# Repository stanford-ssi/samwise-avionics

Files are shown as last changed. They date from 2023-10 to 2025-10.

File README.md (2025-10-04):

# SAMWISE Avionics Repository
Welcome to the SAMWISE GitHub Avionics repository! Here, we (try to) keep the most updated versions of all of our circuit boards accessible to the public.
[Link to the Wiki for onboarding info and general resources](https://github.com/stanford-ssi/samwise-wiki/wiki/Avionics)

## General Layout
Individual boards have their own folders to ease merging of branches. Symbol libraries, footprint libraries, and 3D models are in separate top-level folders. Project templates (for starting out) and jobsets (for project export) are in other top-level folders. Unused, old boards are in the unused_boards folder.

## KiCad Version: 9.0.1 ≤ V < 10.0
Exception: unused boards are version 8.X.X

## List of Relevant Boards (in alphabetical order of folder name)
Note that each major revision generally indicates a new satellite or a significant overhaul of the board and each minor revision generally indicates a board order.
| Board Name | Folder Name |  Current Rev  |  Current Rev Gerber Date  |  Brief Description
| --- | --- | --- | ---  | ---
| ADCS | ADCS/ADCS-v1-samwise  | 01.8 | 09/21/25 | Attitude Control Determination System (ADCS) controller board
| Reaction Wheel Motor Board | ADCS/ADCS-motors-v1-samwise  | 01.1 | 05/28/25 | ADCS reaction wheel controller board
| Battery Board | BatteryBoard | 02.3 | 04/05/25 | Contains battery, charging IC. 2x per satellite
| Flex Deploy Side Panels | FlexDeploySidePanels | 03.3 | 04/22/25 | Deployable side panels, on SAMWISE Y sides (2 sides)
| Groundstation 433 MHz HAT  | Groundstation_433_Hat | 01.3 | 04/07/25 | Raspberry Pi HAT control board for 433 MHz groundstation
| Groundstation 2400 MHz HAT | Groundstation_2400_Hat | 01.6 | 04/06/25 | Raspberry Pi HAT control board for 2400 MHz groundstation
| LT8491 MPPT Module | LT8491_mezzanine | 01.1 | 04/05/25 | Maximum power point tracking (MPPT) module, adapted from Max Holliday's design
| PiCubed | PiCubed/mainboard-v06.4_samwise | 06.4 | 09/21/25 | SAMWISE's master controller board
| MPPT Add-on Board | PiCubed/MPPT_addon_board | 01.4 | 04/06/25 | Holds MPPT modules, attaches to PiCubed
| RPi Interface Board | RPi_Interface | 01.3 | 04/07/25 | HAT board for Raspberry Pi+camera system and 2400 MHz radio
| Stationary X Side Panels | Stationary_X_Panel | 01.6 | 04/26/25 | Stationary (fixed) side panels, on SAMWISE X sides (2 sides)
| Sun Pyramid | sun_sensor_pyramid | 03.2 | 04/07/25 | Holds sun sensors that help determine sun vector for ADCS system
| XY Magnetorquer Coils | Universal_XY_MagTorq | 02.2 | 04/26/25 | XY magnetorquer coil boards, 2 per XY side (4 sides total) in parallel and 5 coils/board in series
| Z Magnetorquer Coils | Universal_Z_MagTorq | 01.1 | 04/07/25 | Z magnetorquer coil boards, 2 per Z side (2 sides total) in parallel and 5 coils/board in series
| Z Side Panel | ZPlus_Panel | 02.4 | 04/22/25 | Z side panels, with antenna + camera on Z+ side. For both Z+ and Z- after thruster removed from Z-

## Guidelines
1. Set up KiCad and GitHub according to the guides in the Wiki.
2. ALWAYS check via `git status` and pull via `git pull` BEFORE making edits. If going into someone else's branch or main, use `git restore <file>` to restore changes before returning to your branch and do NOT commit/push changes without the branch owner's explicit permission. 
3. Create your own branch when making edits. Make pull requests when you have finalized your changes. Do NOT push to main unless you are an AV or team co-lead.
4. To prepare your board for ordering, follow the Board Review and Ordering Procedures linked on the [Notion page](https://ssisatellites.notion.site/Avionics-4ecec69fa093445191cafdee6dff3940). This saves AV/team leads a substantial amount of time, and keeps things consistent/easy to review.
5. Do not edit this README unless you are an AV or team co-lead.

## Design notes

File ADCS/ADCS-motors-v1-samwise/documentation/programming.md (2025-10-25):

Created a repo by forking adcs-flight software
https://github.com/nablaxcroissant/samwise-adcs-motor-flight/tree/main

## I2C Battery Readout
PWR SDA is on pin 45, GPIO 36
PWR SCL is on pin 46, GPIO 37

This means that it lies on I2C bus 0

The IO UART is on GPIO40 for TX and GPIO41 for RX.
This corresponds to UART1 bus.

## may 15 First time testing motor driver code!
The chip enables! Just a SIO gpio pull up and it works as expected.
It draws 21mA at 7V. I'm pretty sure that between 90% and 95% of that is just the driver alone. Could mean that the chip is pulling a lot of power...

I expect it to draw under 10mA at 24V... This means we are good!!!
It is important to note though that this does end up meaning about 80mA power between all 4 motors, even when they are off. When the motors are off its easily fixed - just put them into sleep mode! Will require some extra code probably.

Fault is pulled low...
I figured it out! Its the MOTOR LOCK fault! I just needed to write the spi driver, and it showed me that the 7th bit on register 00 is a motor lock fault. This is probably because the motor is not plugged in.

# Ok that shit is fixed! Was all due to solder issues.

May 30, got SPI communicating!

Now I need to set the correct hall effect configuration
https://shop.faulhaber.com/2610t006b.html
I almost fucked up bad but got really lucky! https://faulhaber.com.cn/fileadmin/Import/Media/AN163_EN.pdf
I was planning to give the hall effects 5V but that could damage the chip. But it looks like 3.3V is actually within the operating range of the hall effects! Yippee!

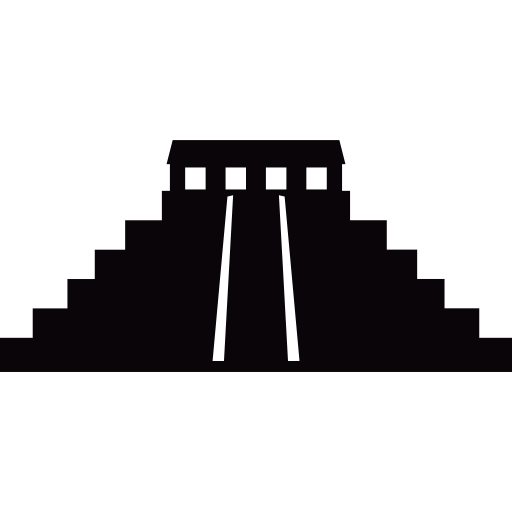
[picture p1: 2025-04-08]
sun_sensor_pyramid/piramide_del_sol.png

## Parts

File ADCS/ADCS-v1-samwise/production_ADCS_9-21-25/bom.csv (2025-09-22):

Designator | Footprint | Quantity | Value | LCSC Part #
C1, C2 | 0603 | 2 | 15pF
C10, C11, C12, C15, C29 | 0603 | 5 | 4.7uF
C13, C14, C16, C21, C23, C28, C31, C35, C37, C42, C43, C44, C45, C46, C47, C5, C59, C60, C63, C7 | 0603 | 20 | 100nF
C17, C18, C24, C33, C9 | 0603 | 5 | 22uF
C19, C20, C22, C25, C30, C34, C38, C39, C48, C51, C66, C8 | 0603 | 12 | 10uF
C26, C32 | 0603 | 2 | 3.3nF
C27, C6, C67 | 0603 | 3 | 1uF
C3, C55, C57, C61, C64 | 0603 | 5 | 10nF
C36, C40, C41, C52, C53, C54 | 0603 | 6 | 3.3uF
C4, C56, C58, C62, C65 | 0603 | 5 | 4.7uF
C49 | 0603 | 1 | 2.2uF
D1 | LED_WS2812B_PLCC4_5.0x5.0mm_P3.2mm | 1 | 1655
D2 | D_SOD-123 | 1 | 1N4151W-E3-08
D3, D4, D6 | DIOM5226X262N | 3 | CMSH1-40M
D5 | 0603 | 1 | GREEN LED
J1, J16, J17, J2 | Molex_505567-0431 | 4 | 505567-0431
J10, J11, J12, J13, J14, J15 | Molex_205338-0002 | 6 | 2053380002
J18, J3 | Molex_505567-0631 | 2 | 505567-0631
J19 | JST_SH_BM04B-SRSS-TB_1x04-1MP_P1.00mm_Vertical | 1 | QWIIC
J20 | SAMTEC_FTSH-105-01-L-DV-007 | 1 | Conn_ARM_JTAG_SWD_10
J4 | Molex_35362-1250 | 1 | 35362-1250
J5 | PinHeader_1x04_P2.54mm_Vertical | 1 | Conn_01x04
J6, J7 | SMA_Amphenol_901-144_horizontal | 2 | Amphenol_901-144
J8 | PinHeader_1x10_P2.54mm_Vertical | 1 | Conn_01x10
J9 | USB_C_Receptacle_XKB_U262-161N-4BVC11 | 1 | USB_C_pycubed
L1 | 0805 | 1 | 3.3uH
L2 | L_2141 | 1 | 3.3uH
Q1, Q2, Q4, Q5, Q6 | DMP2040USS-13 | 5 | DMP2040USS-13
Q3 | SOT-23 | 1 | MMBT2222A
Q7 | SOT-23 | 1 | IRLML2803
R1, R25, R35, R48, R9 | 0603 | 5 | 10k
R10, R11, R12, R15, R53, R56, R64, R65, R66 | 0603 | 9 | 100k
R13 | 0603 | 1 | 73.2k
R14 | 0603 | 1 | 22.1k
R16, R20, R23, R3, R30, R33, R36, R38, R4, R42, R44, R52, R54 | 0603 | 13 | 1k
R17, R21, R22, R29, R31, R32, R34, R37, R41, R43, R45, R46, R5, R50, R51, R59, R6, R60, R61, R68, R70 | 0603 | 21 | 10k
R18 | 0603 | 1 | 5
R2, R24, R47, R8 | 0603 | 4 | 4.7k
R26 | 0603 | 1 | 33
R27, R28 | 0603 | 2 | 27
R39, R40 | 0603 | 2 | 5.1k
R49, R57 | 0603 | 2 | 0
R55 | 0603 | 1 | 4.7M
R62, R63 | 0603 | 2 | 3k
R67 | 0603 | 1 | 4.7k
R69 | 0603 | 1 | 3.3k
R7 | 2512 | 1 | 0.02
SW1, SW2 | BTN_KMR2_4.6X2.8 | 2 | KMR231NG LFS
U1, U6, U8 | QFN-14_MP6551_MNP | 3 | MP6551GQB-Z
U10 | RM3100CB | 1 | RM3100CB
U11 | BMI270 | 1 | BMI270
U12 | Orion_B16 | 1 | Orion B16
U13 | QFN32-5X5MM | 1 | EP2W+
U14, U9 | TSSOP-16_4.4x5mm_P0.65mm | 2 | ADS7830
U15 | SOT-23-5 | 1 | TPS70960DBVR
U2 | RP2350-QFN-80-1EP_10x10_P0.4mm_EP3.4x3.4mm_ThermalVias | 1 | RP2350_80QFN
U3 | SON127P600X500X90-9N | 1 | MR25H40MDF
U4 | ADM1176-1ARMZ-R7 | 1 | RM_10
U5 | PWP14_2P31X2P46-L | 1 | TPS54226PWPR
U7 | TSSOP-14_4.4x5mm_P0.65mm | 1 | TLV1704
Y1 | Crystal_SMD_3225-4Pin_3.2x2.5mm | 1 | ABM8-272-T3

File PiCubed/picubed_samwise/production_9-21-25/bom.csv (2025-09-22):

Designator | Footprint | Quantity | Value | LCSC Part #
C1, C2 | 0603 | 2 | 15pF
C10, C11, C12, C15, C29, C34 | 0603 | 6 | 4.7uF
C13, C14, C16, C21, C24, C28, C3, C40, C45, C46, C47, C48, C49, C5, C50, C7 | 0603 | 16 | 0.1uF
C17, C18, C31, C37, C38 | 0603 | 5 | 22uF
C19, C20, C22 | 1210 | 3 | 10uF
C23, C27, C33, C4 | 0603 | 4 | 1uF
C25, C30, C35, C39, C41, C42, C43, C44, C51, C54, C9 | 0603 | 11 | 10uF
C26, C32 | 0603 | 2 | 3.3nF
C36 | 0603 | 1 | 47nF
C53 | 0603 | 1 | 2.2uF
D1 | LED_WS2812B_PLCC4_5.0x5.0mm_P3.2mm | 1 | 1655
D2 | DO-214AC | 1 | CDBA240LL
D3, D7, D8 | DIOM5226X262N | 3 | CMSH1-40M
D4 | PWRDI-123 | 1 | DFLS130L
D5 | 0603 | 1 | GREEN LED
D6 | D_SOD-123 | 1 | 1N4151W-E3-08
J1 | Molex_503182-1852 | 1 | 503182-1852
J10, J17 | Molex_35362-0450 | 2 | 35362-0450
J11 | PinSocket_2x09_P2.54mm_Vertical | 1 | MPPT board
J12, J15 | Molex_35362-0550 | 2 | 35362-0550
J13 | USB_C_Receptacle_XKB_U262-161N-4BVC11 | 1 | USB_C_pycubed
J14 | PinHeader_1x08_P2.54mm_Horizontal | 1 | Conn_01x08_Horizontal
J16, J18, J8, J9 | 1985807 | 4 | 1985807
J19 | Molex_35362-0650 | 1 | 35362-0650
J2 | SAMTEC_FTSH-105-01-L-DV-007 | 1 | Conn_ARM_JTAG_SWD_10
J20, J21 | Molex_35362-0750 | 2 | 35362-0750
J22 | JST_SH_BM04B-SRSS-TB_1x04-1MP_P1.00mm_Vertical | 1 | QWIIC
J3, J4 | Molex_35362-0850 | 2 | 35362-0850
J5 | Molex_35362-1250 | 1 | 35362-1250
J6 | Molex_35362-0950 | 1 | 35362-0950
J7 | SMA_Amphenol_901-144_horizontal | 1 | Amphenol_901-144
JP1 | SolderJumper-2_P1.3mm_Open_Pad1.0x1.5mm | 1 | Jumper_2_Open
JP2, JP3 | SolderJumper-2_P1.3mm_Bridged_Pad1.0x1.5mm | 2 | Jumper_2_Bridged
L1 | polarized | 1 | 3.3uH
L2 | L_2141 | 1 | 3.3uH
L3 | SDE06004A-680K | 1 | 68uH
L4 | L_2510 | 1 | 1uH
Q10, Q21 | DMP2040USS-13 | 2 | DMP2040USS-13
Q5, Q9 | SOT-23 | 2 | IRLML2803
Q6 | SOT-23 | 1 | MMBT2222A-TP
R1, R18 | 0603 | 2 | 330k
R10 | 0603 | 1 | 20k
R11, R12, R15, R27, R38, R46, R60, R61, R62, R68, R69, R70, R75 | 0603 | 13 | 100k
R13 | 0603 | 1 | 73.2k
R14 | 0603 | 1 | 22.1k
R16 | 0603 | 1 | 49.9k
R17 | 0603 | 1 | 510k
R19 | 2512 | 1 | 0.27
R2 | 0603 | 1 | 110k
R20, R23, R26, R3, R4, R56, R6, R63 | 0603 | 8 | 1k
R21, R22, R25, R28, R29, R31, R34, R35, R44, R45, R5, R51, R53, R54, R55, R57, R71, R72, R73, R74, R76, R77, R78 | 0603 | 23 | 10k
R33, R58, R59 | 0603 | 3 | 3.3k
R36 | 0603 | 1 | 560
R39, R40 | 0603 | 2 | 5.1k
R50, R82 | 0603 | 2 | 0
R64 | 0603 | 1 | 4.7M
R65 | 0603 | 1 | 33
R66, R67 | 0603 | 2 | 27
R79, R80 | 0603 | 2 | 3k
R8 | 2512 | 1 | 0.02
R9 | 0603 | 1 | 121k
SW1, SW2 | BTN_KMR2_4.6X2.8 | 2 | KMR231NG LFS
U1 | SOT-23-5 | 1 | TPS70960DBVR
U16 | Relay_PE014006 | 1 | PE014006
U17 | QFN50P400X400X100-25N-D | 1 | BQ25883RGER
U2 | RP2350-QFN-80-1EP_10x10_P0.4mm_EP3.4x3.4mm_ThermalVias | 1 | RP2350_80QFN
U21 | TPS7A4501DCQT | 1 | TPS7A4501DCQT
U23 | RFM98PW | 1 | RFM98PW
U3 | SON127P600X500X90-9N | 1 | MR25H40MDF
U4 | ADM1176-1ARMZ-R7 | 1 | RM_10
U5 | PWP14_2P31X2P46-L | 1 | TPS54226PWPR
U6 | MSOP-12_MSE | 1 | LT3652HVIMSE#PBF
U7 | TSSOP-14_4.4x5mm_P0.65mm | 1 | TLV1704
Y1 | Crystal_SMD_3225-4Pin_3.2x2.5mm | 1 | ABM8-272-T3

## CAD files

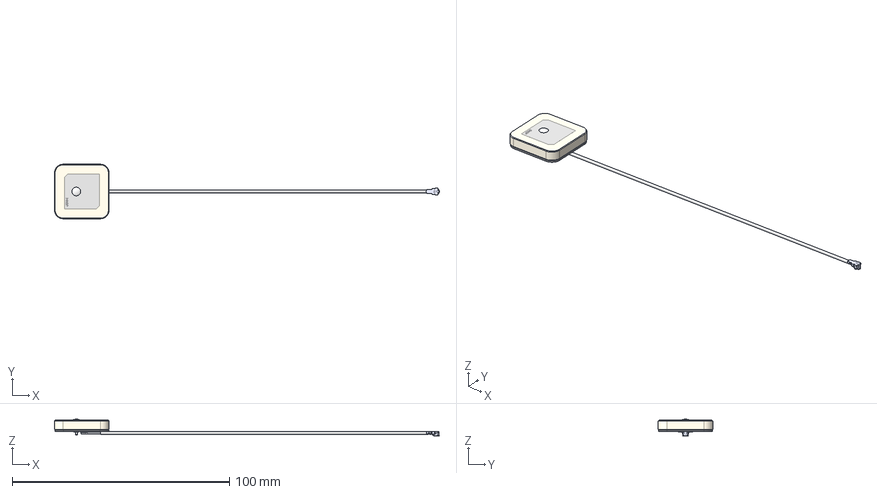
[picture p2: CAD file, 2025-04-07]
3D_models/ssi_antenna/WPC_25A.step
177.0 x 25.1 x 7.67 mm
001517C100000A WLP.2450.25.4 Patch
100211I010011A_WPC.25A PCB
300115C010000A_1.37 Gray Cable
204511G000000A_IPEX MHFHT. 1.37

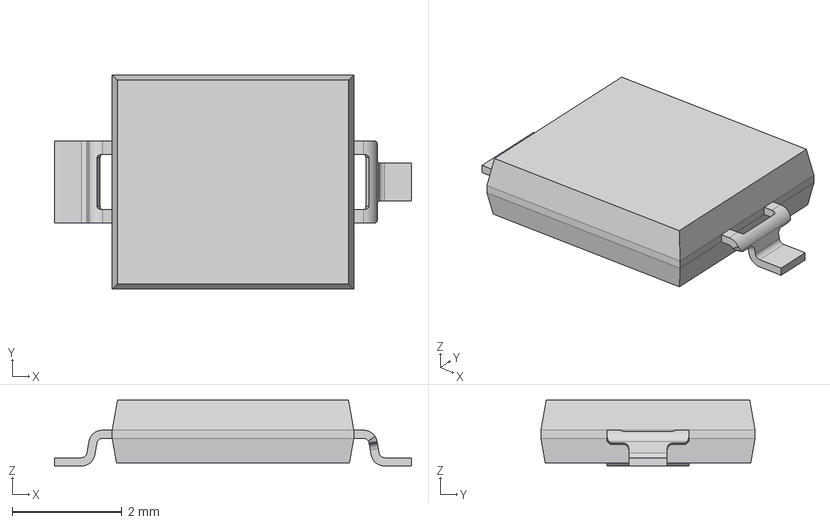
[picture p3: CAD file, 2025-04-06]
3D_models/ssi_diode/SFH_2430.step
6.50 x 3.90 x 1.20 mm

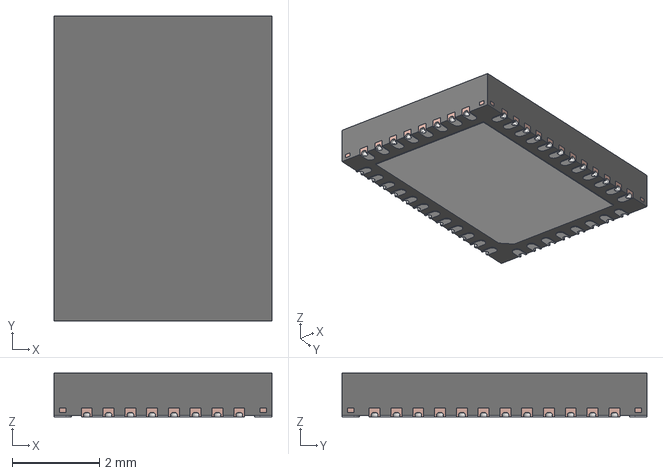
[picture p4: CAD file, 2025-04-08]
3D_models/ssi_IC/MCT8316Z-Q1.step
5.00 x 7.00 x 1.00 mm
FRAME

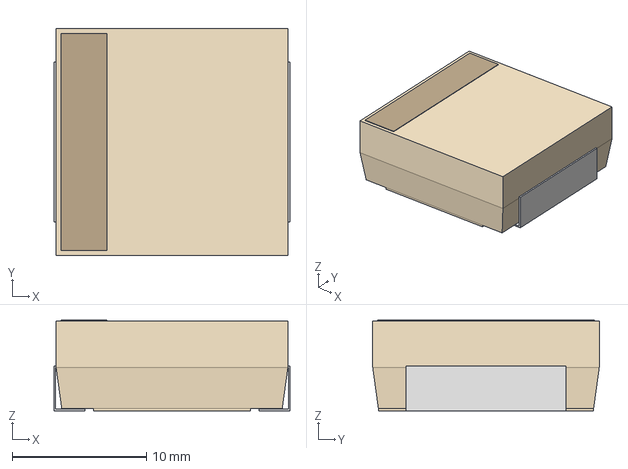
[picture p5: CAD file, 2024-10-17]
3D_models/ssi_inductor/SRP1770CC.step
17.6 x 16.9 x 6.76 mm

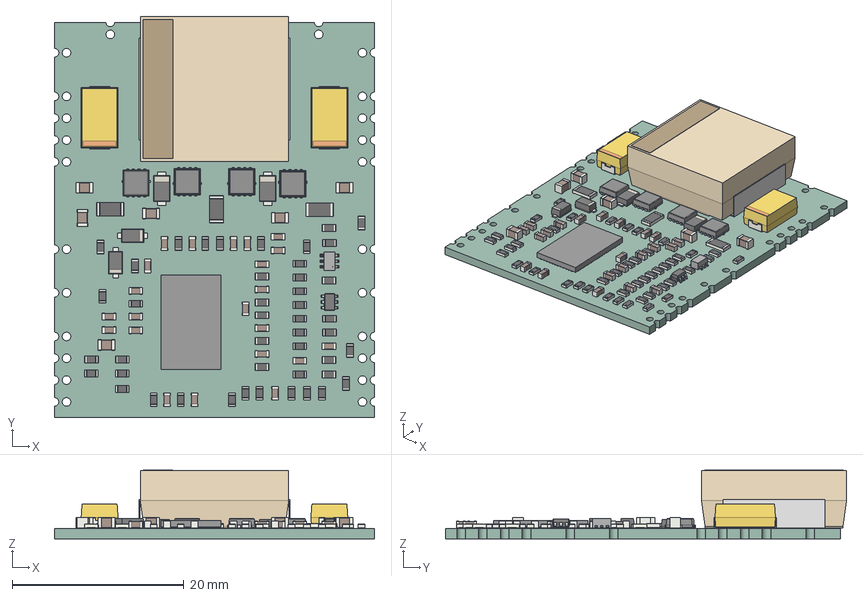
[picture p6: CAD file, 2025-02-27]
3D_models/ssi_misc/LT8491.step
37.2 x 46.7 x 8.02 mm
R_0603_1608Metric x 45
C_0805_2012Metric x 6
C_0603_1608Metric x 22
D_PowerDI_123 x 2
SOT_363_SC_70_6
(Unsaved) x 5
R_1206_3216Metric x 3
D_SOD_123F x 2
CP_EIA_7343_30_AVX_N x 2
LT8491-mezzanine_PCB

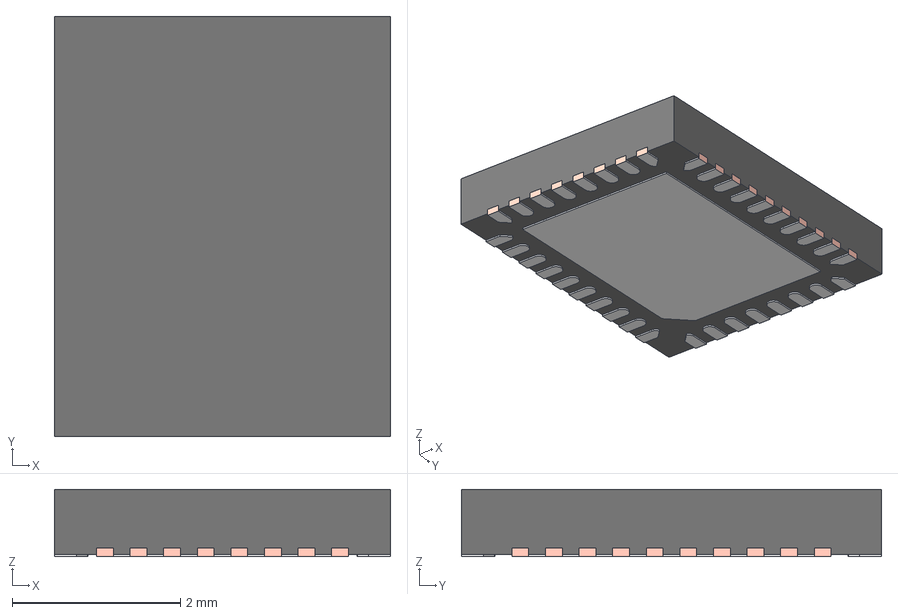
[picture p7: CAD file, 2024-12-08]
3D_models/ssi_reaction_wheel/REE0036A.stp
4.00 x 5.00 x 0.8 mm
BODY-QFN
FRAME-REE0036A

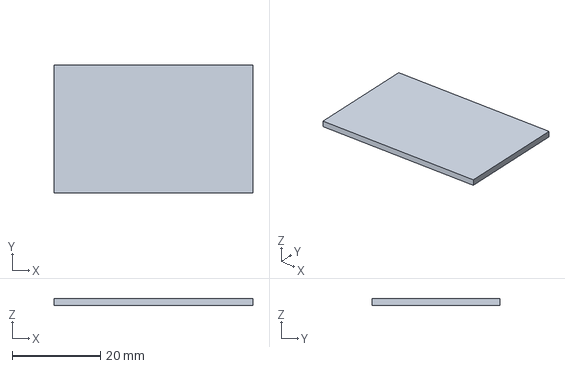
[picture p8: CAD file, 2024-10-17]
3D_models/ssi_solar/SM141K08TFV.step
45.0 x 29.0 x 1.50 mm

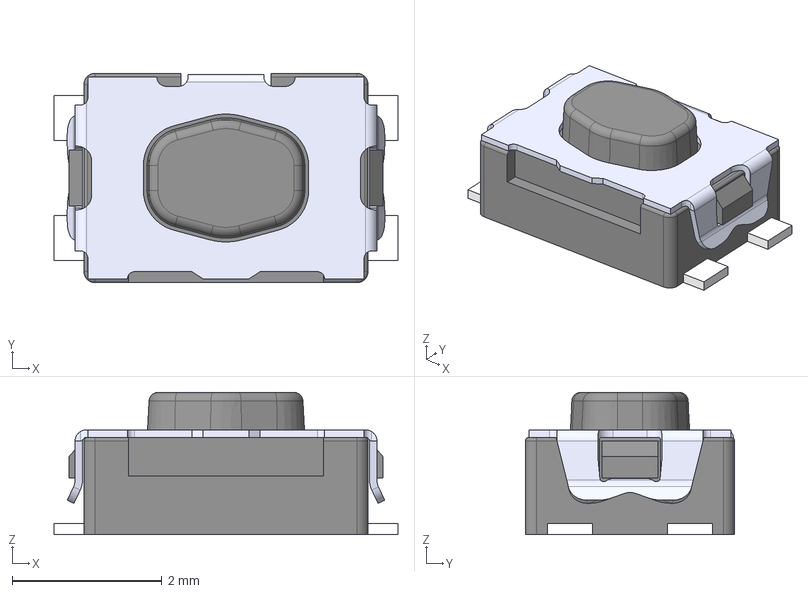
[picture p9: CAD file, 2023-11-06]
3D_models/ssi_switch/KMR221GLFS.step
4.60 x 2.80 x 1.90 mm

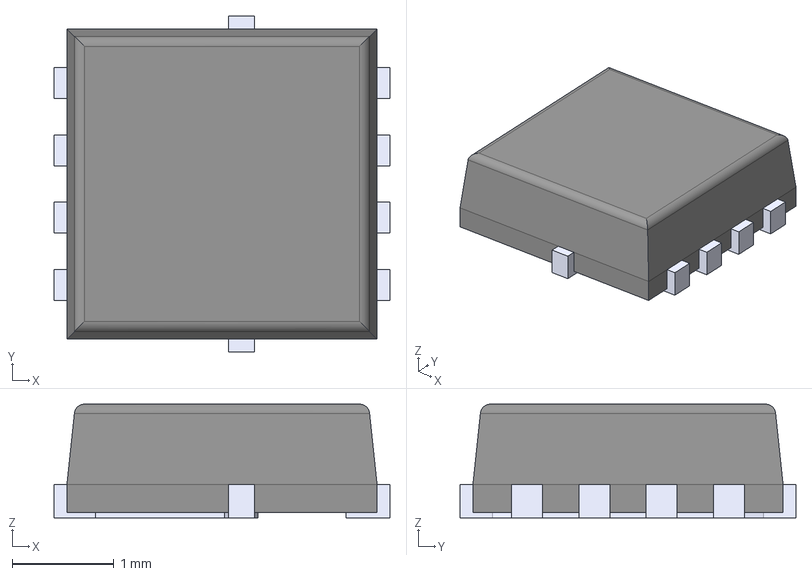
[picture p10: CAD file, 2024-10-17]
3D_models/ssi_transistor/SIS128LDN-T1-GE3.step
3.30 x 3.30 x 1.12 mm

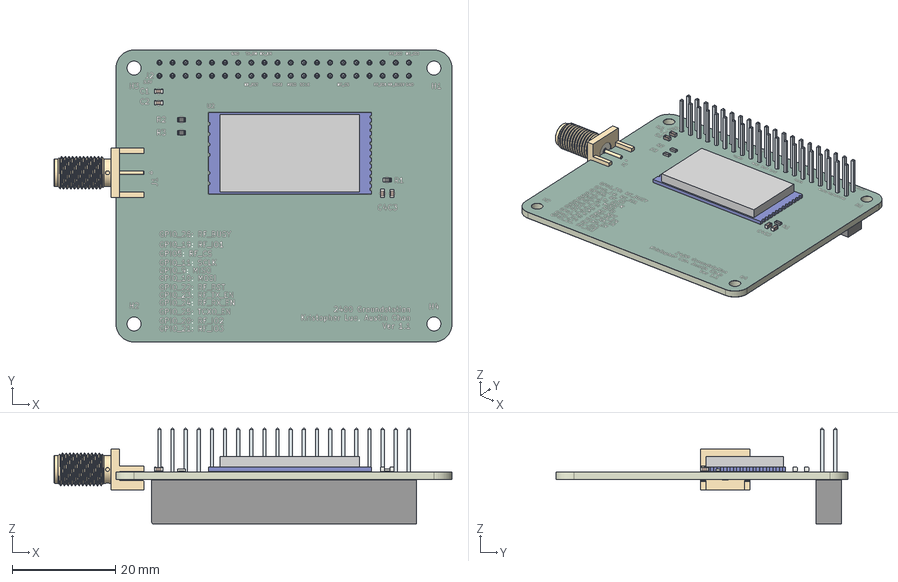
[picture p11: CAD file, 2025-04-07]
Groundstation_2400_Hat/Groundstation_2400_Hat_v1.1_2025-04-06.step
77.0 x 56.5 x 18.5 mm
C_0603_1608Metric x 4
R_0603_1608Metric x 3
LORA1280F27-TCXO
SMA_Amphenol_132289_EdgeMount
LeadsArray
Groundstation_2400_Hat_silkscreen
Groundstation_2400_Hat_soldermask
Groundstation_2400_Hat_PCB

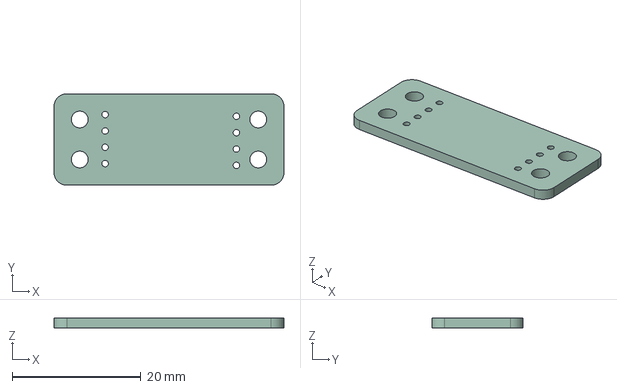
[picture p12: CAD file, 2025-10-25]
magnetometer_extern/magnetometer_extern/magnetometer_extern.step
35.8 x 14.2 x 1.51 mm

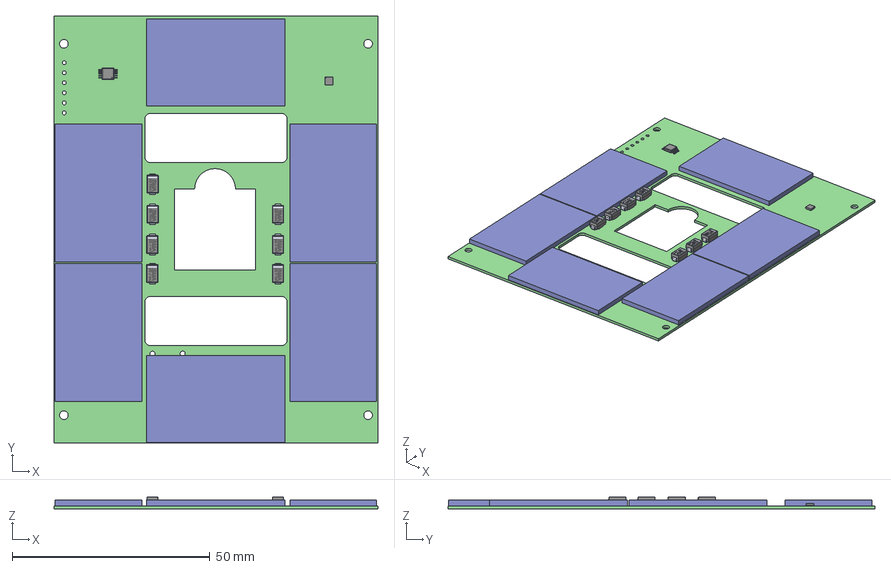
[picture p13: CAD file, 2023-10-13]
MagnetorquerSidePanels/X_Y_Panels.step
82.0 x 108.0 x 3.15 mm
X_Y_Panels PCB

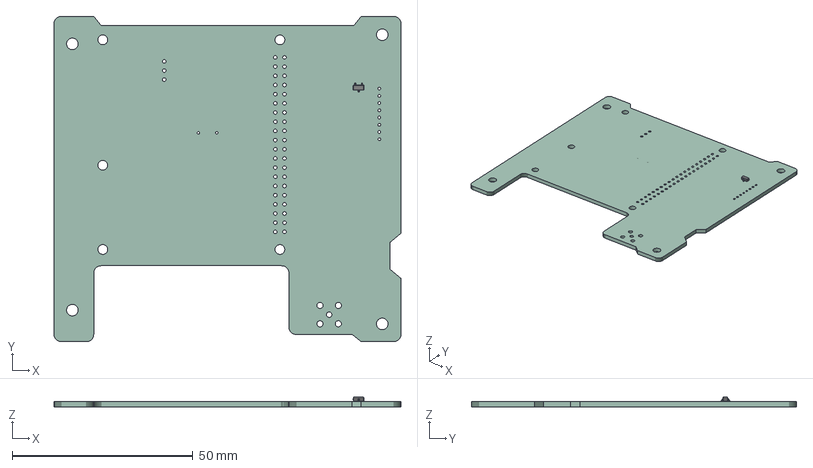
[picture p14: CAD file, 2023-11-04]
RPi_Interface/RPi_interface.step
96.0 x 90.0 x 2.84 mm
RPi_interface PCB

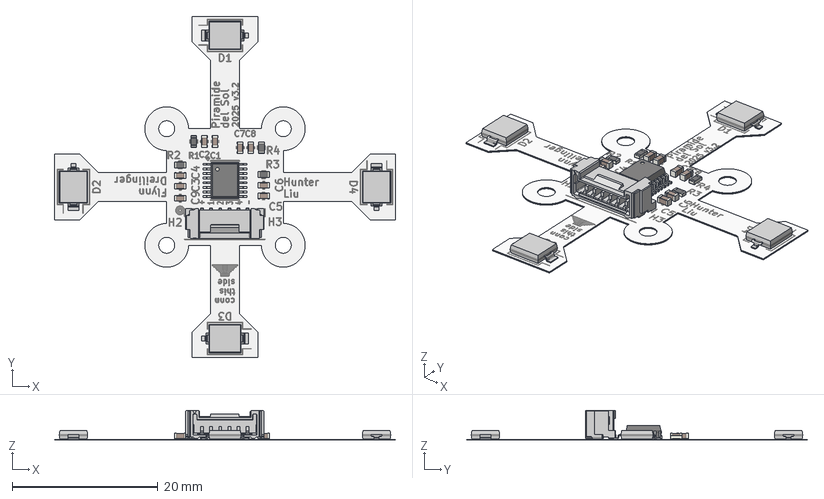
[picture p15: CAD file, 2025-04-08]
sun_sensor_pyramid/Piramide_Del_Sol_v3.2_2025-04-07.step
46.8 x 46.8 x 4.13 mm
SFH_2430 x 4
C_0603_1608Metric x 9
R_0603_1608Metric x 4
SSOP-16_3.9x4.9mm_P0.635mm
Piramide_Del_Sol_silkscreen
Piramide_Del_Sol_soldermask
Piramide_Del_Sol_PCB

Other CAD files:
Universal_XY_MagTorq/Coil_Panel_XY_v2.2_2025-04-26.step
Universal_Z_MagTorq/Coil_Panel_Z_v1/Coil_Panel_Z_v1.1_2025-04-07.step
3D_models/ssi_antenna/AP_25M.step
3D_models/ssi_diode/M7.step
3D_models/ssi_IC/ADM1176-1ARMZ-R7.step
3D_models/ssi_IC/ATSAMD51J20A-AU.step
3D_models/ssi_IC/BMI270.step
3D_models/ssi_IC/DRV8830DGQ.STEP
3D_models/ssi_IC/EP2W.step
3D_models/ssi_IC/HHM1589D1.step
3D_models/ssi_IC/LORA1280F27-TCXO.step
3D_models/ssi_IC/LT8491IUKJ#PBF.step
3D_models/ssi_IC/MP6551GQB-Z.step
3D_models/ssi_IC/MR25H40MDF.step
3D_models/ssi_IC/MSOP-12_MSE_LIT.step
3D_models/ssi_IC/OPT3001DNPT.step
3D_models/ssi_IC/Orion_B16.step
3D_models/ssi_IC/PWP0014E.step
3D_models/ssi_IC/PX1120S.step
3D_models/ssi_IC/RFM95W v5.step
3D_models/ssi_IC/RFM98PW_RFM95PW.STEP
3D_models/ssi_IC/RP2350_QFN80.step
3D_models/ssi_IC/SOT363_1P3X2P15_DIO.step
3D_models/ssi_IC/TPS7A4501DCQT.step
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

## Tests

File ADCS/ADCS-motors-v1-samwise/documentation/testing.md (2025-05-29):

Testing:

## Saturday May 3
Board was finished on tuesday, and I went in with the goal of getting working power traces

- [x] Completed 3.3V
1. Nothing was happening
- Checked pullup resistor for continuity - looked good but resoldered just in case
- Eventually realized that the actual pin on the ic was not soldered on
- It then output voltage and behaved as a switch but it was at 0.763V
    - this is exactly the voltage when no feedback is applied
- fixed the feedback and it worked

- [x] Completed 1.1V
- Again, we got voltage, but the waveform was super weird
- I checked pins to see if they were behaving right
- VREG-AVDD was meant to be at 3.3V but it was at ~1.1 V
    - The resistor was a 22k instead of a 33
    - Swapped it out and it worked!6

Issues Remaining:
Board is drawing ~200mA - way more than we would expect when all chips are off
First attempted debug is using thermal camera
## Sunday May 4
- Ok Thermal Camera shows that most of the power loss is in the rp2350 and the regulator ic. So I am stumped.

## Tuesday May 
Tested impedance between 3.3 V and GND. It read an even 20.5Ω. I am going to look for resistors of that value on the board.
Nothing worked. The short was constant everywhere we tested.
Took heat gun and removed the MCU - fixed?
Put it back on - broken again!!

Checking which pin the short is on... 1.1V is shorted by 60 olms on pin 32
Also 10 is shorted to ground. 10 and 32 are shorted with basically 0 ohlm

Pin 76 is 42 ohlm. 60 is 26 ohlm. Between 76 and 60 is 27 ohlm

51 and 50 also shorted
1.8 ohlm on pin 52 - motor RX pin!!! Got shorted to power during testing... maybe broke all the io logic power pins

## Friday May 9
Met with Pete today! Oscillator issue was almost definitely due to short circuit on the pins between them. Board may be busted.
Worked on other board (1.1V regulator not turning on) issue was not shorts - it was poorly connected circuits. Almost an entire side of the chip was not connected to the terminals. Pretty darn not good. Less likely to be damaged than the other board - power was not getting in so it was unlikely to have damaged anything.

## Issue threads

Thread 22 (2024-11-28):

PiCubed PCB top layer USB Connector J13 Pin A4 reduced clearance

pete4radio, 2024-11-28:
A short trace to VBUS reduces the solder clearance and suggestion that it be moved slightly to the right.
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

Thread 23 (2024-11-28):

PiCubed PCB Top Silkscreen lower right says old version

pete4radio, 2024-11-28:
The title block and file names are 06c but the board is labelled V06b.  The "b"  board had a SAMD51, this one, the "c" has the RP2350B.
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

daheehee, 2024-12-07:
resolved

Closed 2024-12-07.

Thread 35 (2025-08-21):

Fix watchdog timer

lundeen06, 2025-08-21:
@millywy found that using a 6V regulator (part # ???, datasheet ???) fixed the issue with the watchdog. We need to add the corrected circuit to all boards that use it, which includes picubed, adcs, and the motor board.

Closed 2025-09-24.

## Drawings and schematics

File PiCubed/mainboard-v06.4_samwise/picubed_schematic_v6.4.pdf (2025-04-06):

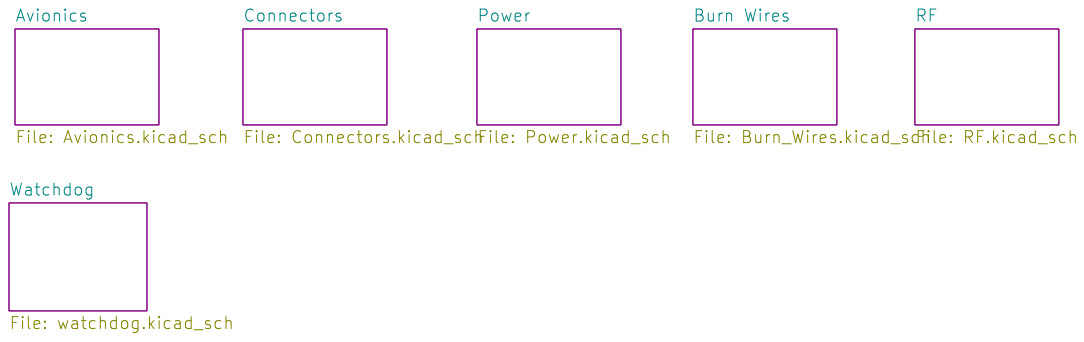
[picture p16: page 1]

Id: 1/7 Title: PiCubed Mainboard

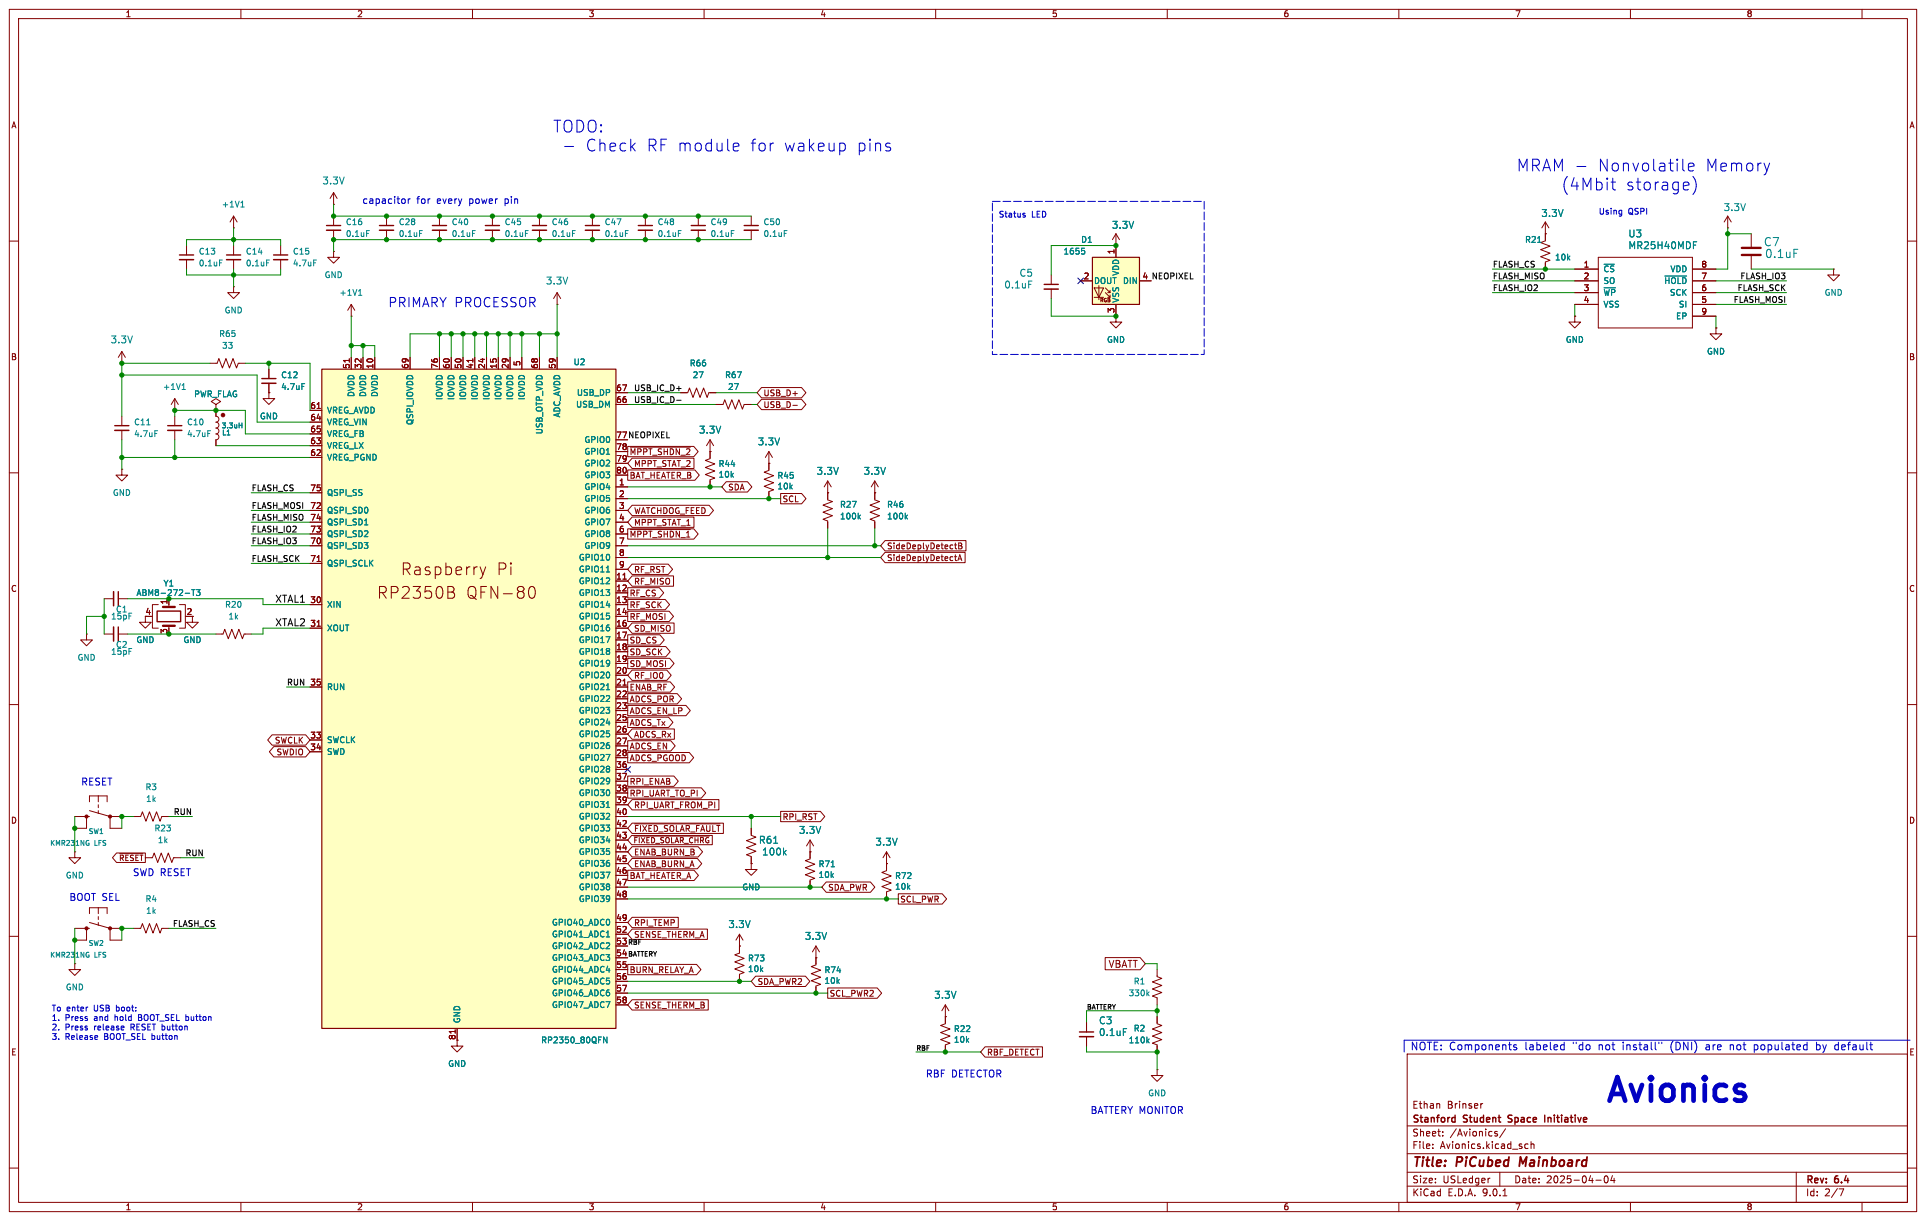
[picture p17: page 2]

TODO: - Check RF module for wakeup pins

To enter USB boot: 1. Press and hold BOOT_SEL button

2. Press release RESET button
3. Release BOOT_SEL button

Id: 2/7 Title: PiCubed Mainboard

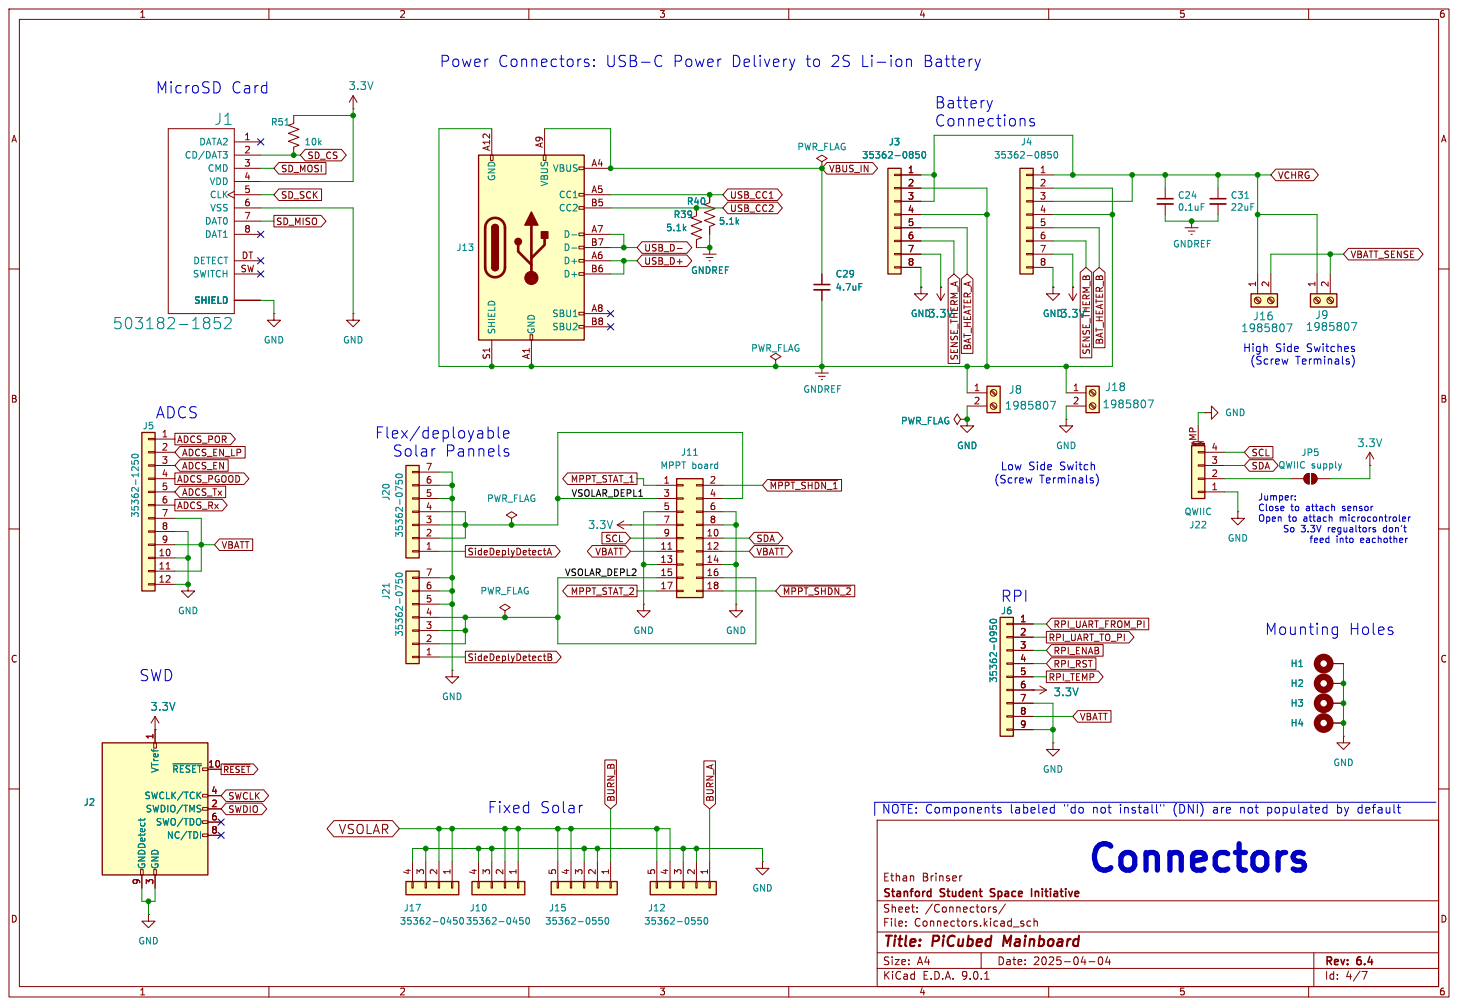
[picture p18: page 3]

3 ~{RESET}10 SWCLK/TCK 4 SWDIO/TMS 2 SWO/TDO 6 NC/TDI 8

Id: 4/7 Title: PiCubed Mainboard

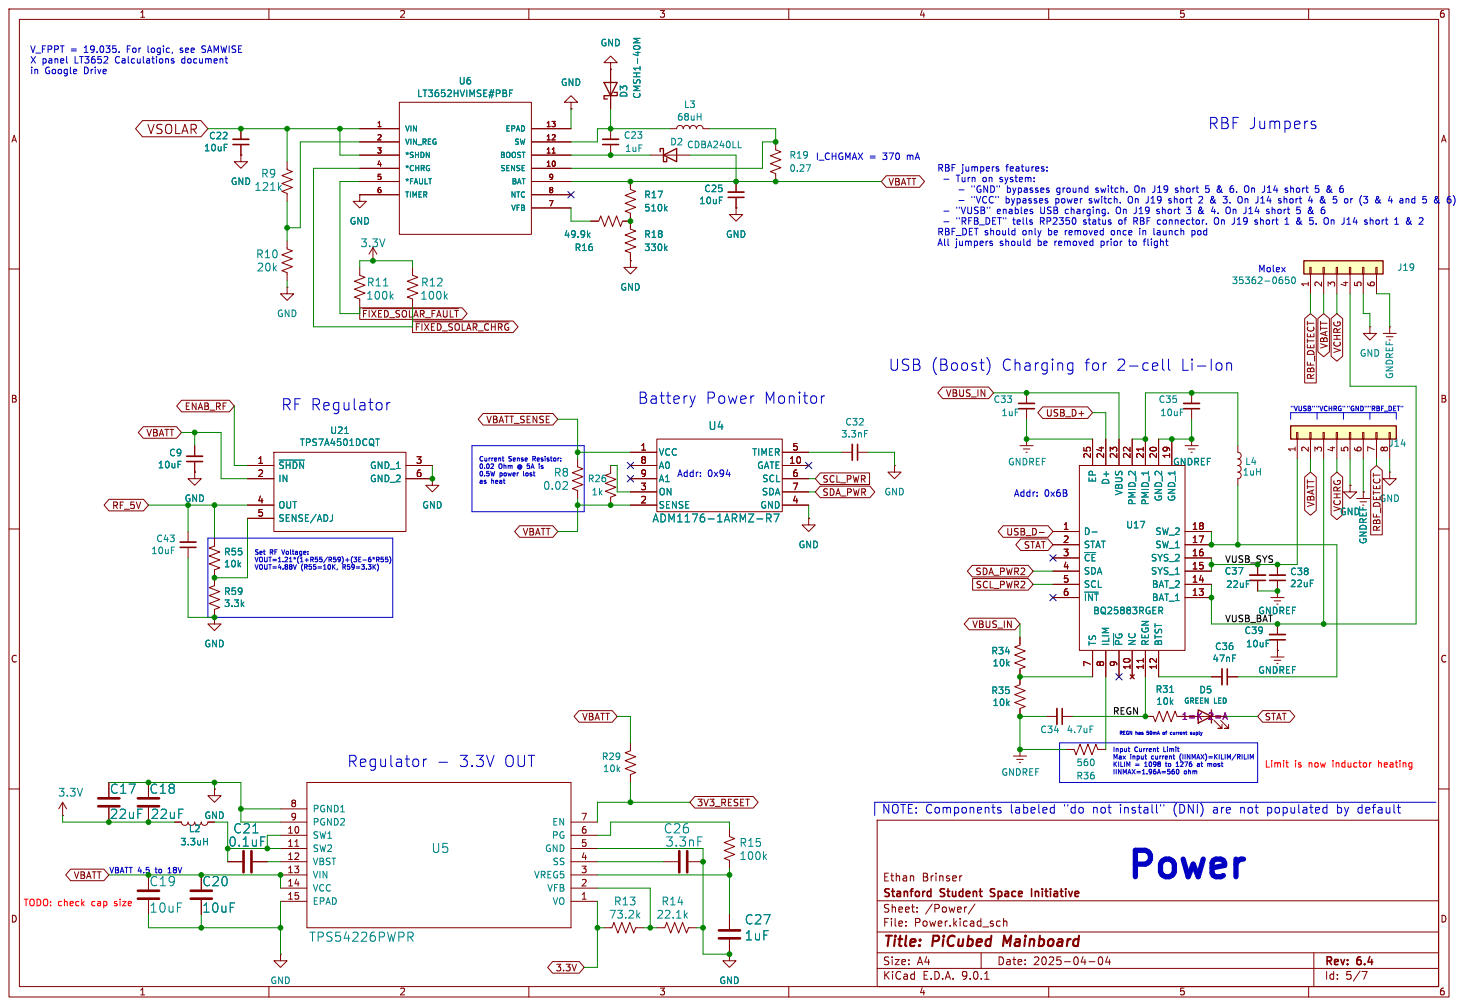
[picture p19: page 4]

"VUSB" Molex RBF jumpers features: - Turn on system: - "GND" bypasses ground switch. On J19 short 5 & 6. On J14 short 5 & 6

8 VBUS 23 ~{PG} 9 NC 10 GND_2 20 GND_1 19 GNDREF C25

- "VCC" bypasses power switch. On J19 short 2 & 3. On J14 short 4 & 5 or (3 & 4 and 5 & 6)

"VCHRG" Current Sense Resistor: 0.02 Ohm @ 5A is 0.5W power lost as heat TODO: check cap size

8 VBUS 23 ~{PG} 9 NC 10 GND_2 20 GND_1 19 U17 BQ25883RGER GND

KILIM = 1098 to 1276 at most

Id: 5/7 Title: PiCubed Mainboard

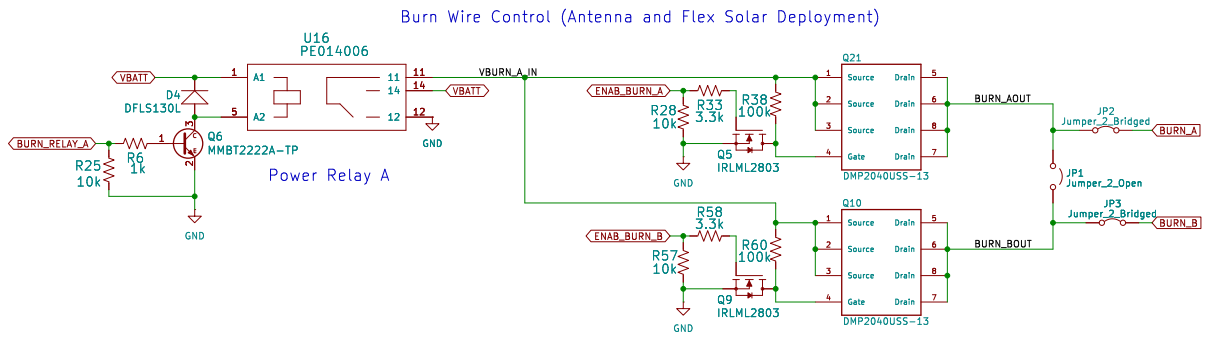
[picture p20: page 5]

Burn Wire Control (Antenna and Flex Solar Deployment)

Id: 6/7 Title: PiCubed Mainboard

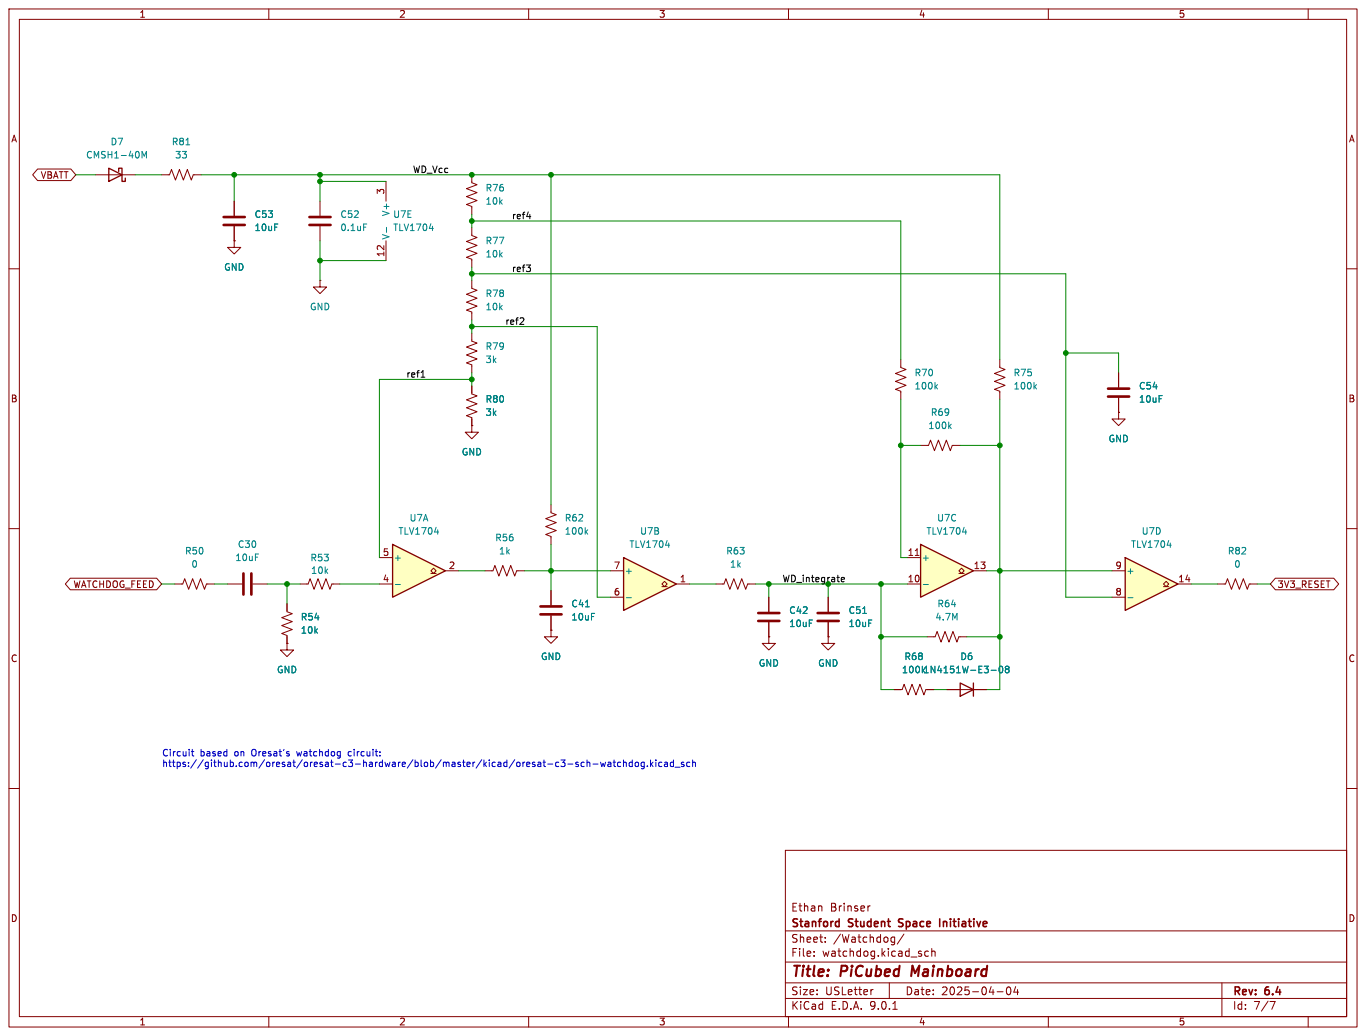
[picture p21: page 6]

Id: 7/7 Title: PiCubed Mainboard

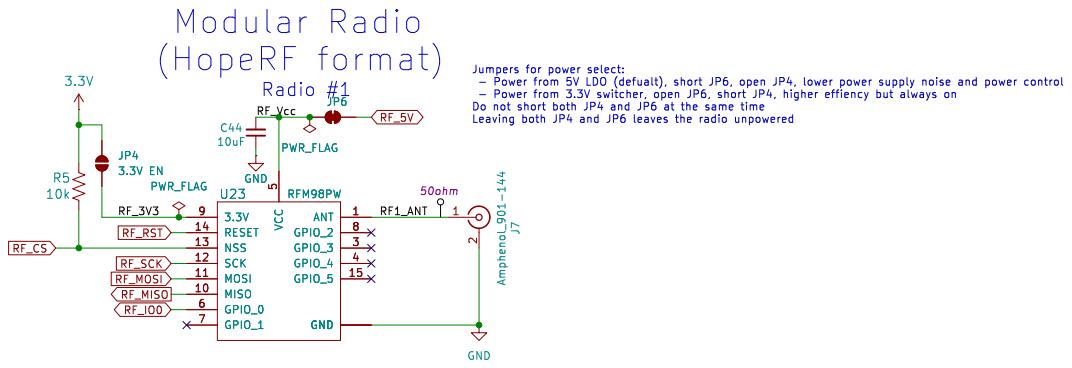
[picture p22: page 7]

Leaving both JP4 and JP6 leaves the radio unpowered

Id: 7/7 Title: PiCubed Mainboard

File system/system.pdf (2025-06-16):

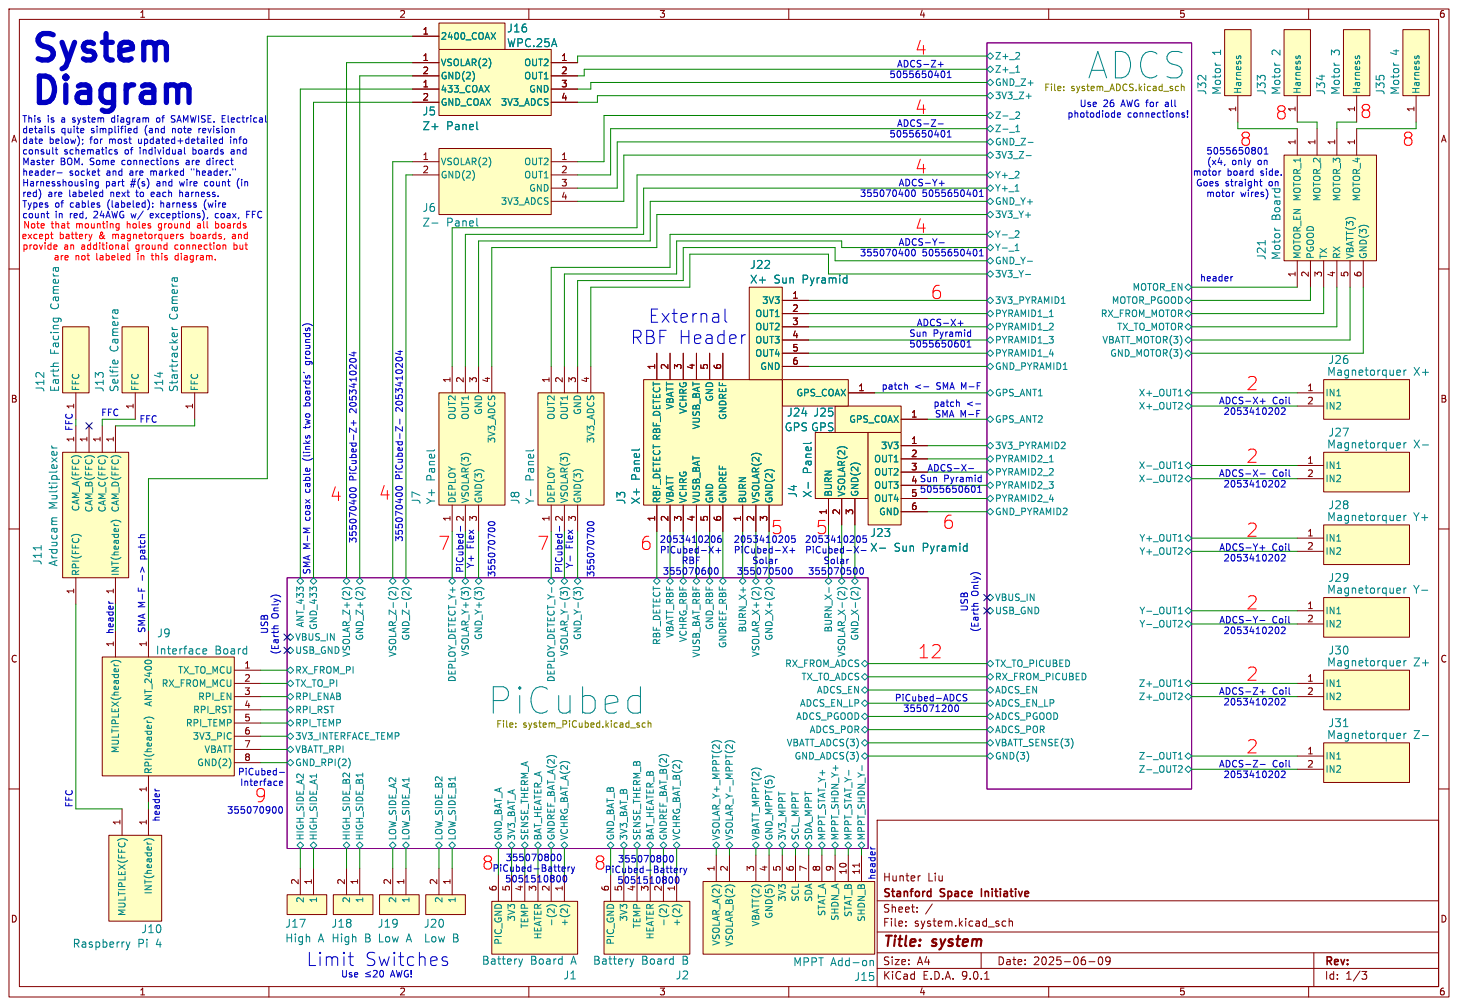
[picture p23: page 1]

1 J21 Motor Board MULTIPLEX(header) 1 ANT_2400

6 J3X+ Panel 3V3 1 OUT1 2 OUT2 3 OUT3 4 OUT4 5 GND 6 J22 X+ Sun Pyramid

1 VSOLAR(2) 2 GND(2) 3 J4X- Panel GPS_COAX J25 1 GPS

2 J17 High A INT(header) 1 MULTIPLEX(FFC) 1 J10 Raspberry Pi 4 +(2) 1 -(2) 2 HEATER

355070800 PiCubed-Battery 5051510800 Limit Switches

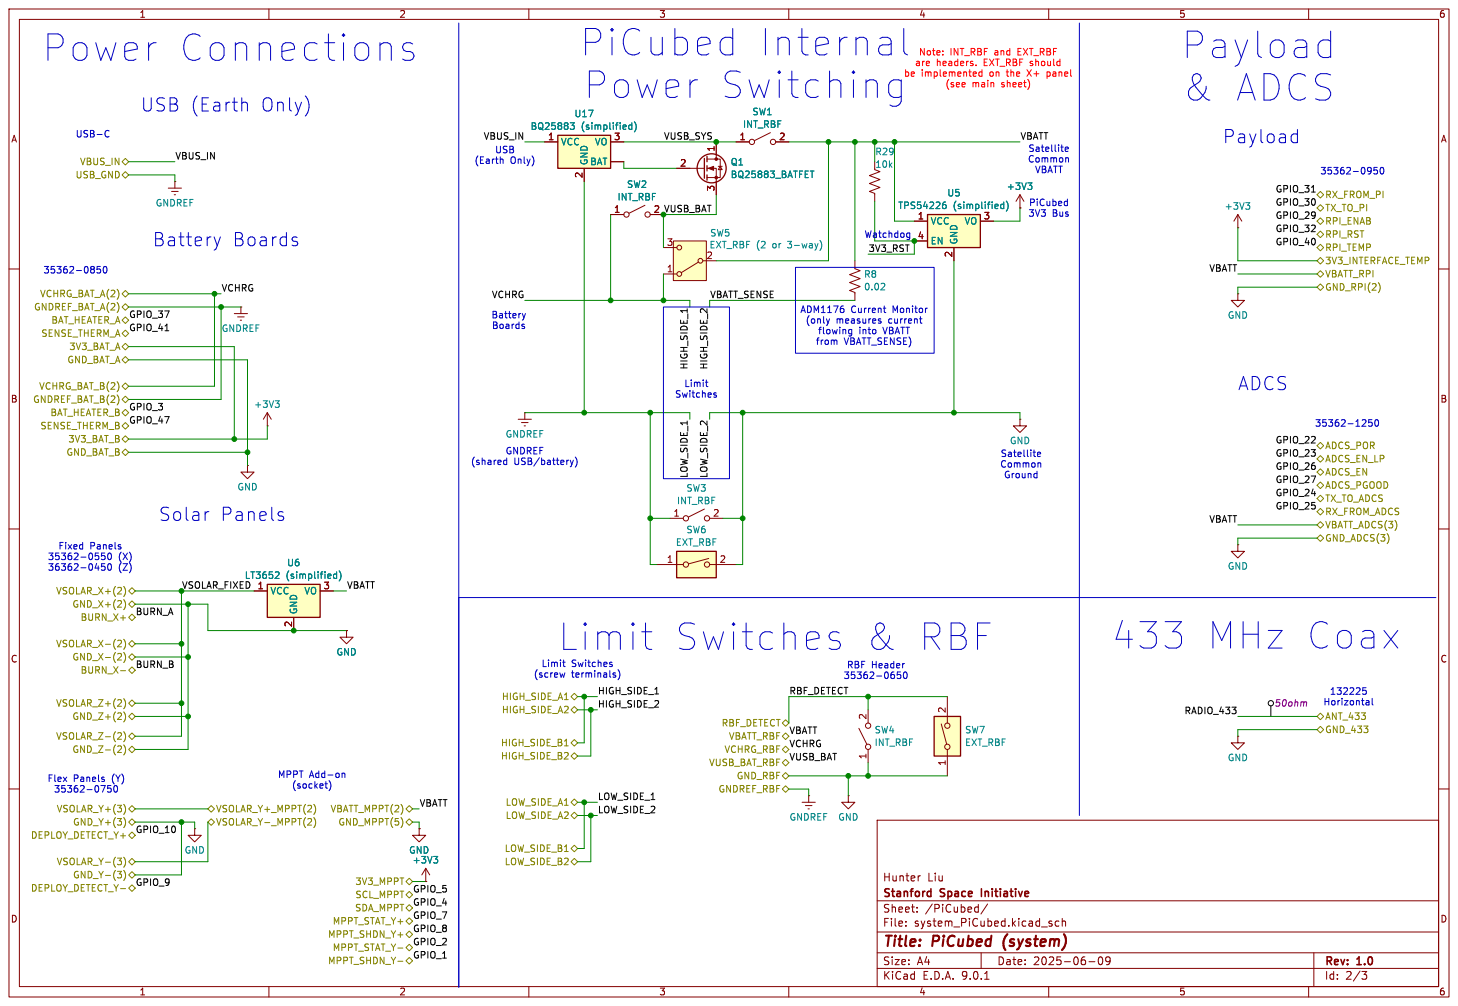
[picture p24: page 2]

PiCubed Internal
Power Switching
USB (Earth Only) MPPT Add-on

(see main sheet)PiCubed

2 VO 3 BAT U17 BQ25883 (simplified) 1 2 SW6 EXT_RBF VCC 1 GND

3V3 Bus Battery Boards GNDREF

Limit Switches Limit Switches & RBF

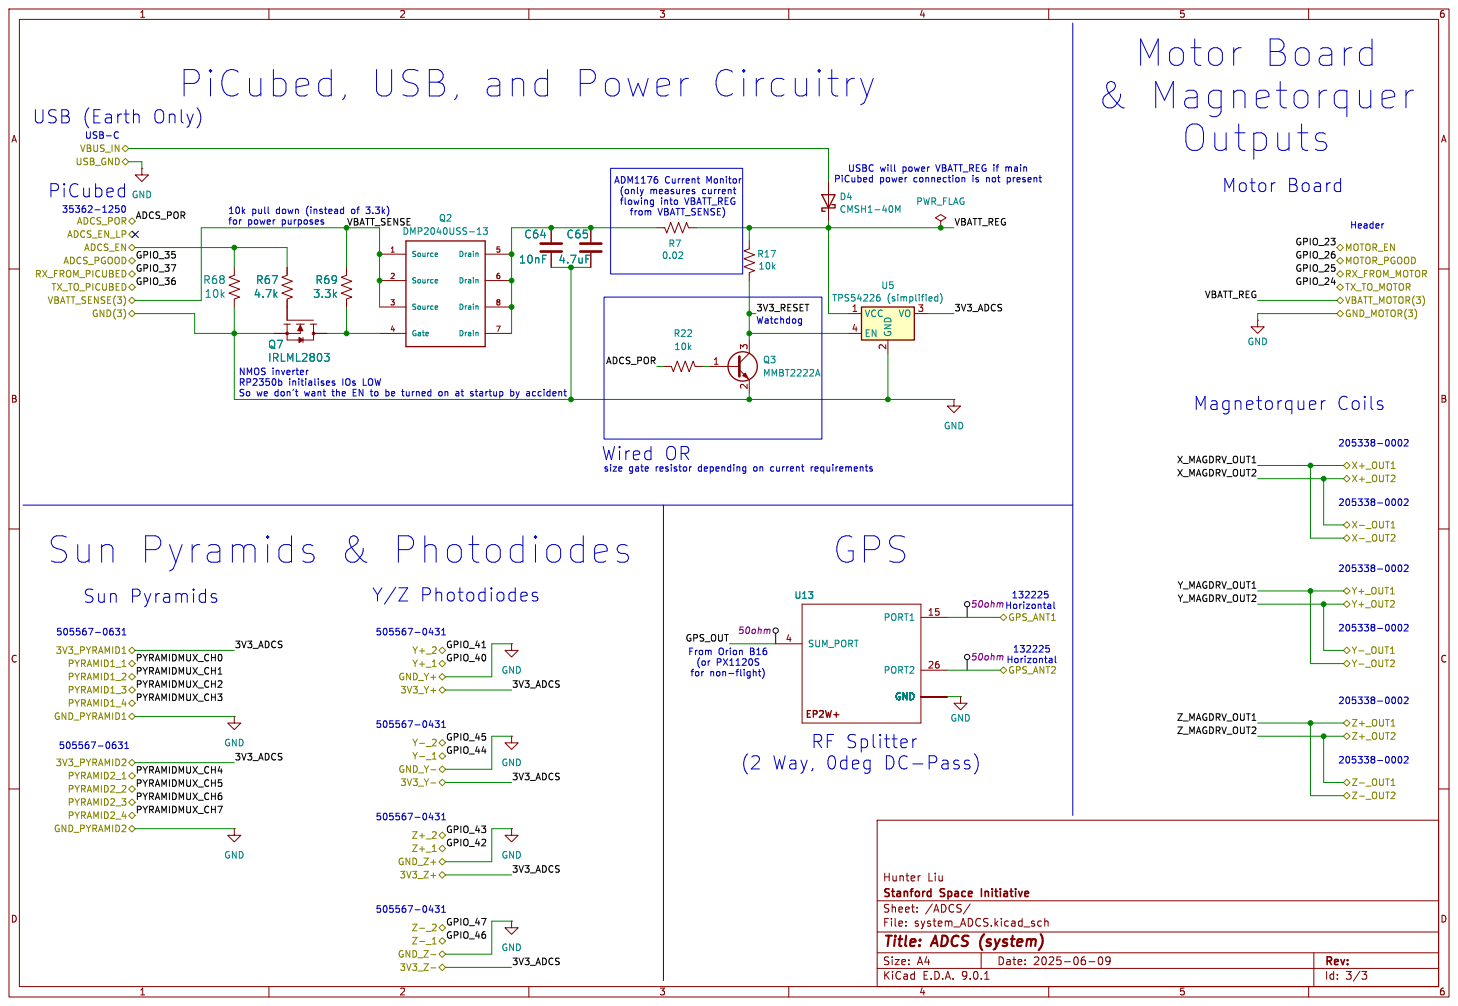
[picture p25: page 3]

PiCubed, USB, and Power Circuitry

So we don't want the EN to be turned on at startup by accident 35362-1250
ADCS_POR
VBATT_SENSE(3) ADCS_PGOOD
RX_FROM_PICUBED
TX_TO_PICUBED

3 2 Q3 MMBT2222A GND GND GND GND

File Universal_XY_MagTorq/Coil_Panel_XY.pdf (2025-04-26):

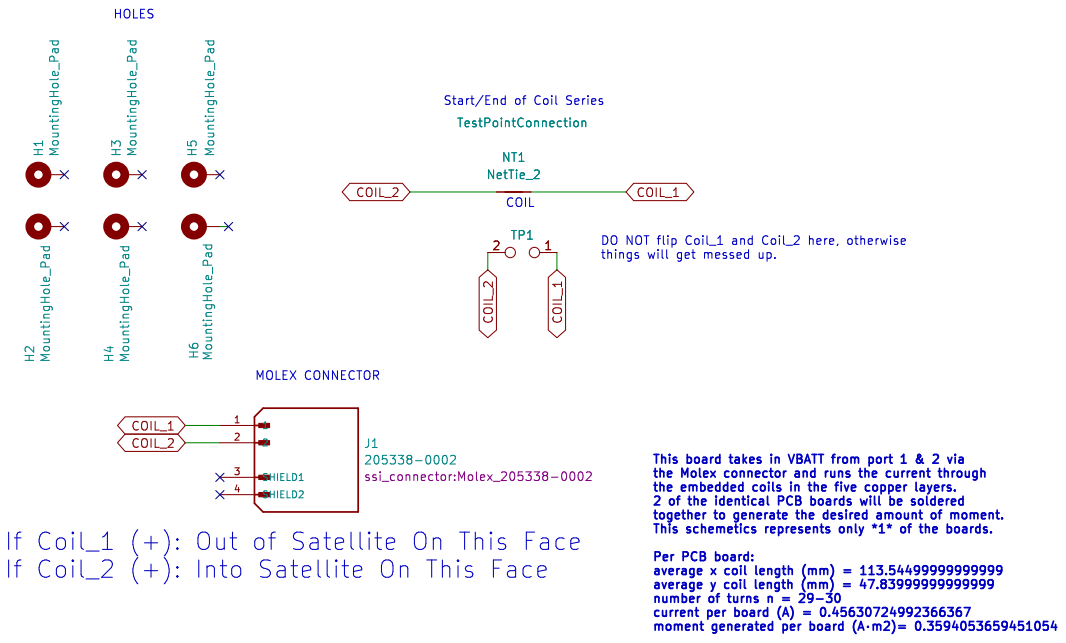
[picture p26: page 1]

things will get messed up. HOLES

current per board (A) = 0.45630724992366367 moment generated per board þÿ(A"Åm2)= 0.3594053659451054 DO NOT flip Coil_1 and Coil_2 here, otherwise

This board takes in VBATT from port 1 & 2 via
the Molex connector and runs the current through

together to generate the desired amount of moment. This schemetics represents only *1* of the boards. Per PCB board: average x coil length (mm) = 113.54499999999999

average y coil length (mm) = 47.83999999999999 number of turns n = 29-30

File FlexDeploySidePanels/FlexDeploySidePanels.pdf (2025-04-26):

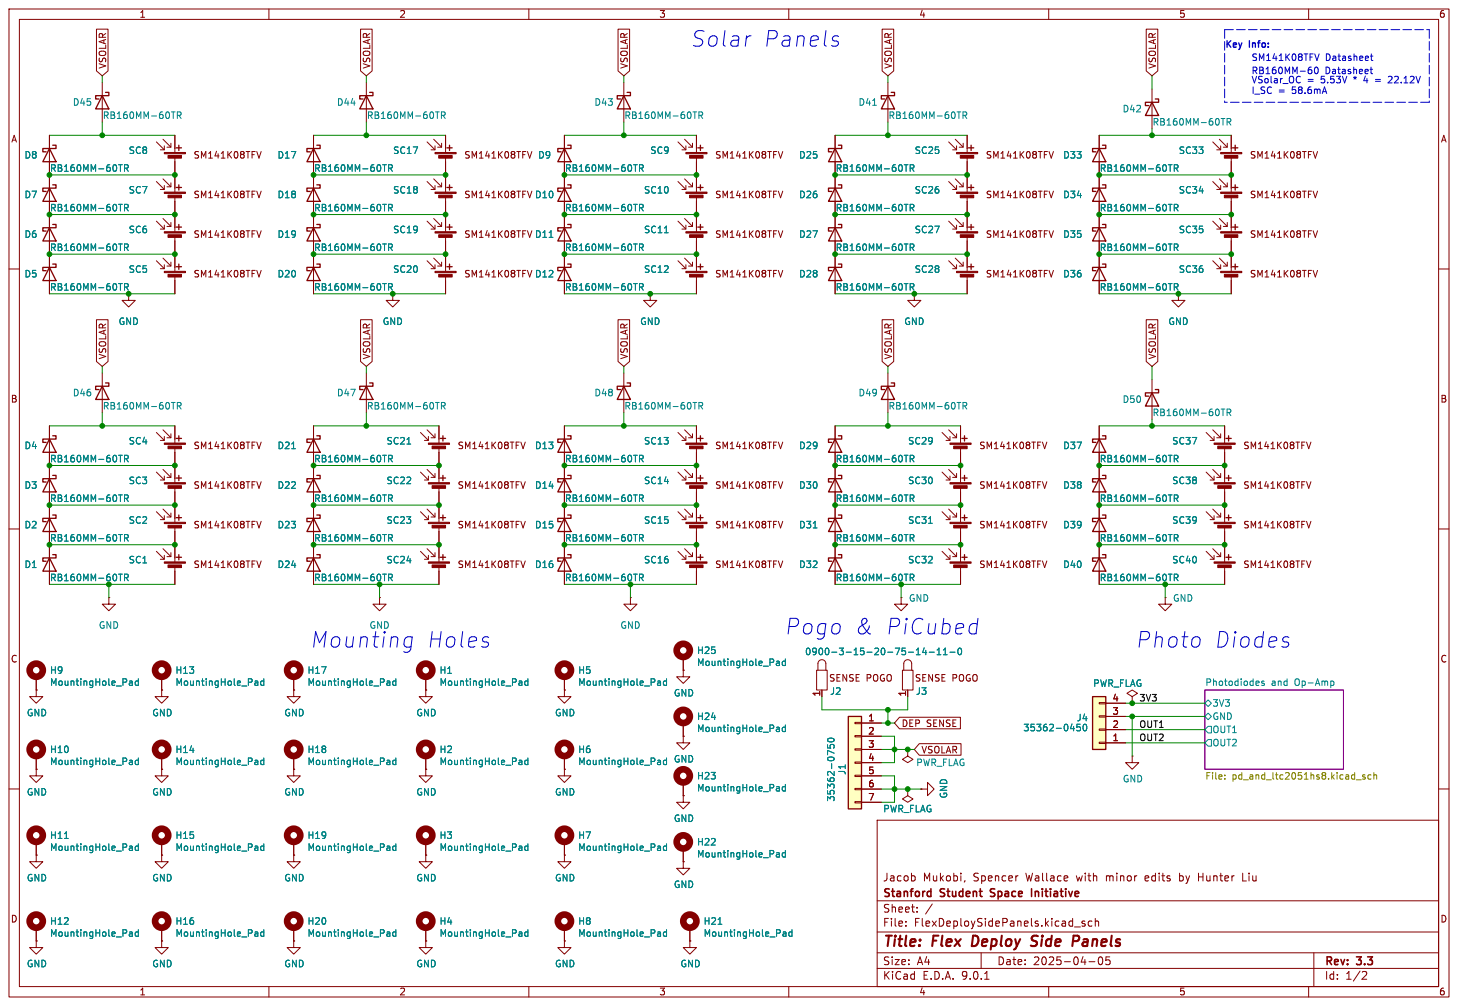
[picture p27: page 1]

3V3 Photo Diodes Pogo & PiCubed Mounting Holes

Id: 1/2 Title: Flex Deploy Side Panels


Id: 2/2 Title: Flex Deploy Side Panels

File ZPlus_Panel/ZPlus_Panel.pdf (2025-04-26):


1 2 AE1 UHF_Dipole_Antenna SC1 SM101K07TF SC2 SM101K07TF D0 CDBA240LL-HF GND D2 CDBA240LL-HF D1 CDBA240LL-HF D6 CDBA240LL-HF GND H4 H8 GND D4 CDBA240LL-HF GND D3 CDBA240LL-HF SC3 SM101K07TF SC5 SM101K07TF SC6 SM101K07TF GND

2 D5 CDBA240LL-HF D3 CDBA240LL-HF SC3 SM101K07TF SC4 SM101K07TF SC5 SM101K07TF SC6 SM101K07TF D4 CDBA240LL-HF D6 CDBA240LL-HF D1 CDBA240LL-HF D2 CDBA240LL-HF D0 CDBA240LL-HF SC1 SM101K07TF SC2 SM101K07TF


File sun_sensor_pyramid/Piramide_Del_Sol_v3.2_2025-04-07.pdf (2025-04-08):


current flow from X
panel (see there for design) and associated

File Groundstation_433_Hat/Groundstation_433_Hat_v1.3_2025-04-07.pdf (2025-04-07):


(Mounts Directly on Board)

(powers relay switches) Labels Represent

To flip relays
(two in parallel)
to switch between Tx/Rx To switch between

Id: 1/2 Title: 433MHz Ground Station Board


This Sheet Contains Internal Board Connections

Connect to PA/LNA

LNA/PA Dual Control

2N7002 ON IPC Semiconductor 1.11 2N7002 7351B mm

100k +5V GND Q1
GND

Id: 2/2 Title: 433MHz Ground Station Board

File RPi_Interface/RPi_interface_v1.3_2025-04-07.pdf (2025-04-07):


RPi Payload Power Converter
ENAB_RPI RF_RX_EN

high to enable power to Raspberry Pi! EN_Low < 0.4V, PB23 Low = 0V

EN_High > 1.5V, PB23 High = 3.3V
used to keep the pin from floating when pycubed powered off, uses about 33uW

Higher input capacitance
to reduce effects from
radio LDO inrush current (also C14 near LDO). Limited

TCXO on by default whenever ENAB_RF

Id: 1/1 Title: Raspberry Pi Interface Board

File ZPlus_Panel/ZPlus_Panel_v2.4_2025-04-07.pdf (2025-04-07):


1 2 AE1 UHF_Dipole_Antenna SC1 SM101K07TF SC2 SM101K07TF D0 CDBA240LL-HF GND D2 CDBA240LL-HF D1 CDBA240LL-HF D6 CDBA240LL-HF GND H4 H8 GND D4 CDBA240LL-HF GND D3 CDBA240LL-HF SC3 SM101K07TF SC5 SM101K07TF SC6 SM101K07TF GND

2 D5 CDBA240LL-HF D3 CDBA240LL-HF SC3 SM101K07TF SC4 SM101K07TF SC5 SM101K07TF SC6 SM101K07TF D4 CDBA240LL-HF D6 CDBA240LL-HF D1 CDBA240LL-HF D2 CDBA240LL-HF D0 CDBA240LL-HF SC1 SM101K07TF SC2 SM101K07TF



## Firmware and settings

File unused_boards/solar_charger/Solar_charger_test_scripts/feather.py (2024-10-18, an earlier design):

'''Print data over serial port'''

import time
import board
import adafruit_ina260
import busio

SOLAR_AMMETER_ADDRESS = 0x41 # Addresses from I2C scan
BATTERY_AMMETER_ADDRESS = 0x45

# Initialize I2C and sensor
i2c = busio.I2C(board.SCL, board.SDA)
solar_ammeter = adafruit_ina260.INA260(i2c, SOLAR_AMMETER_ADDRESS)
batt_ammeter = adafruit_ina260.INA260(i2c, BATTERY_AMMETER_ADDRESS)

# Logging loop
while True:
    # Collect data
    solar_current = solar_ammeter.current
    solar_voltage = solar_ammeter.voltage
    solar_power = solar_ammeter.power

    batt_current = batt_ammeter.current
    batt_voltage = batt_ammeter.voltage
    batt_power = batt_ammeter.power

    # Print data in comma-separated format
    print(f"{time.monotonic()},{solar_current},{solar_voltage},{solar_power},{batt_current},{batt_voltage},{batt_power}")
    
    # Delay to maintain the 100ms interval
    time.sleep(0.1)

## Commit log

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2023-10-22 Added flex pcbs
    [solar-panel-side-X-plus.kicad_pcb, solar-panel-side-X-plus.kicad_sch]
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2023-11-04 updated 3D models on battery magnetorquer and pycubed boards, added unfinished RPi interface board
    [18650 battery.STEP, 1985807.step, 2053380006.stp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]
2023-11-04 created flex pcb side panel project
    [solar-panel-side-X-plus.kicad_pcb, solar-panel-side-X-plus.kicad_sch]
2023-11-04 fixed files for feather radio board
    [FeatherRadioAdapter.kicad_pcb, FeatherRadioAdapter.kicad_sch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]
2023-11-04 added flex deploy side panels
    [FlexDeploySidePanels.kicad_pcb, FlexDeploySidePanels.kicad_sch]
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2023-11-06 fixed batteryboard 3D model issues
    [batteryboard.kicad_pcb]
2023-11-06 added 3D models to magnetorquer side panel boards
    [2053380002.step, 2053380006.step, 2053380006.stp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]
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2023-11-10 added gate resistor to burn wire circuit
    [Avionics.kicad_sch, Burn_Wires.kicad_sch, Bus_Protection.kicad_sch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]
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2023-11-12 added resister to burn wire circuit
2023-11-17 Added R6 resistor on burn wire circuit to PCB layout
2023-11-17 Pycubed footprint fixes, RPi interface board fixes 20231116
    [PRT-21570.step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]
2023-12-03 flipped LORA module to correct orientation, new gerbers
    [RPi_interface-B_Cu.gbl, RPi_interface-B_Mask.gbs, RPi_interface-B_Paste.gbp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]
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2024-01-22 Connector Canges
    Changed on schematic:
    JTAG to standard JTAG 10 pin
    Added ADCS connector
    [Connectors.kicad_sch]
2024-01-22 Added solar connector to PyCubed schematic
    Need to verify quantity and connections
    [35362-0250.stp, Connectors.kicad_sch]
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2024-01-23 fixed some footprints
    [Connectors.kicad_sch, RF_and_GPS.kicad_sch]
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2024-01-31 cleanup
    Removed traces to nothing
    put connectors in spots that might work. Needs checking and connections
    [Avionics.kicad_sch, mainboard.kicad_pcb]
2024-02-03 schematic changes to power
    Added MPPT power module
    Increased USB charging input current limit
    [Connectors.kicad_sch, Power.kicad_sch]
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2024-02-09 miscilanious fixes
    Fixed some footpritns not matching library footprints. Also did some other things. Will need to check 50 Ohm trace, though it is now a net class.
    [Power.kicad_sch, RF_and_GPS.kicad_sch, mainboard.kicad_pcb]
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2024-02-17 MPPT board connector added to Pycubed
    This only changes the schematic. Footprint needs to be added.
    Also resolved a conflict with IO resources between the MPPT circuit and the RGB LED
    [Avionics.kicad_sch, Connectors.kicad_sch, MPPT_addon_board.kicad_sch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]
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2024-02-24 added extra i2c circuit, still need to connect to MPPT connector
    [Bus_Protection.kicad_sch, Connectors.kicad_sch, Power.kicad_sch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]
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2024-02-28 Everything is connected
    Also no clearance violations
    Still some courtyard overlaps that should not mater
    [Avionics.kicad_sch, Bus_Protection.kicad_sch, Connectors.kicad_sch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]
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2024-03-02 Lots of changes
    ADCS connector size increased
    X solar panel connectors now have burn connection
    Added second burn mosfet output
    Touched up RF LDO regulator
    Fliped RPi UART signals
    Likely some other small things.
    [Avionics.kicad_sch, Burn_Wires.kicad_sch, Connectors.kicad_sch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]
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2024-03-05 small fixes
    [mainboard.kicad_pcb]
2024-03-05 fixed usbc diff pair (where possible)
    [mainboard.kicad_pcb]
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2024-04-10 first version of MPPT add-on board to be printed
    [I2C_Bus_Protection.kicad_sch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]
2024-04-27 Some updates
    Issues fixed:
    Fixed Radio power selection. No longer need to cut traces.
    Quality of life:
    Brought in board edges to help with wiring where available.
    Move RPi connector up to get it out of corner of frame.
    Move R27 (RPi enable pulldown) to be with other components so it is harder to not paste or place it. (Value should still be changed)
    General cleanup:
    Touched up RF regulator as part of the Radio power selection. Section could be rotated 90 degrees clockwise to further improve. (ground path between radio and regulator)
    Touchup around top left battery connector.
    [Avionics.kicad_sch, Burn_Wires.kicad_sch, Bus_Protection.kicad_sch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]
2024-04-27 new addon changes to switch SDA and SDL pins
    [MPPT_addon_board.kicad_pcb]
2024-04-27 added deeper edge cuts to provide more room for wires
    [MPPT_addon_board.kicad_pcb]
2024-04-27 more updates
    Big changes:
    Added deployment sense lines
    Removed Radio IO4 connection
    Swapped all GND symbols to be standard KiCAD one and removed it from the library
    Other:
    Changed R27 value to be more common
    Made all the "K" in resistor values be capitalized
    Cleaned up a few things
    [Avionics.kicad_sch, Burn_Wires.kicad_sch, Bus_Protection.kicad_sch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]
2024-05-01 More pycubed updates
    Modified USB-C footprint to better match MFG's recommended. (Requires 4 DRC exclusions for pad to hole)
    Moved USB-C connector 2 mm right to allow for more clearance for the RBF connector on side panel.
    Changed Flex solar connector to match the flex solar board pinout
    A bit of general touchup
    [Connectors.kicad_sch, mainboard.kicad_pcb]
2024-05-04 Orientation and labeling changes
    Rotate 180deg the battery connector at the top right to make latch easier to access. Update silkscreen accordingly
    Fix some minor DRC errors
    Added MPPT and on board pins partial labeling
    Increased font size for connector labeling.
    [mainboard.kicad_pcb]
2024-05-04 More small pycbuded changes
    Fixed title block
    Fixed Watchdog datasheet link (was broken)
    Reduced watchdog tie in resistor value
    Replaced an old ground symbol
    Cleaned up some labeling
    Checked some capacitor ratings
    Changed fixed solar regulator input capacitor voltage rating to be higher. All capacitors should be checked and have values put in fields
    Small silkscreen edits
    [Avionics.kicad_sch, Burn_Wires.kicad_sch, Bus_Protection.kicad_sch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]
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2024-05-05 Changed RPi and ADCS connectors to 9 pins
    This is to prevent the battery board from being plugged into the RPi or ADCS spot (this actually happened once). The ADCS and RPi ports are now nearly identical and should be able to interchange with only loss of functionality.
    [Connectors.kicad_sch, mainboard.kicad_pcb]
2024-05-08 added BJT for shutdown pins connecting PyCubed and MPPT
    [MPPT_addon_board.kicad_pcb, MPPT_addon_board.kicad_sch]
2024-05-08 adding version, name, and text on circuit board
    [MPPT_addon_board.kicad_pcb, MPPT_addon_board.kicad_sch]
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2024-05-11 Copy over of 7 pin sherlock connector footprint
    From commit number 9e5dbb5
    From Branch: flexdeploy
    [35362-0750.step]
2024-05-11 Imported 5 pin molex connector
    Files copied over from commit: 8db27e6
    From Branch flexdeploy
    [35362-0550.step]
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2024-05-11 More pycubed updates
    Updated all connectors to match other boards
    Cleaned up some footprints that had silkscreen running over pads.
    Touched up connector footprints (courtyard and pin 1 indicators)
    Fixed most of the courtyard overlaps
    Some other light touchups on layout
    [Connectors.kicad_sch, mainboard.kicad_pcb]
2024-05-11 Added second Z panel connection
    Also some additional cleanup
    [Connectors.kicad_sch, mainboard.kicad_pcb]
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2024-05-14 Rotated and Moved the uSD card holder to hopefully have better access to it from X- hole
    [mainboard.kicad_pcb]
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2024-05-15 Lots of changes
    Some of these changes were made on schematic on previous commit, but now on the layout
    Update connector pinouts:
    - Battery
    - Z solar
    - Y flex solar
    - Local RBF
    Added QWIIC connector
    Increased max current sense to 5A by changing R8
    Changed C19, C20 to be 10uF
    Changed C22 & C19 & C20's footprint and specs to all match
    Added some power flags
    Made sense resistor have a 4 wire kelvin connection
    Silkscreen cleanup
    General cleanup
    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
    [Avionics.kicad_sch, Burn_Wires.kicad_sch, Bus_Protection.kicad_sch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]
2024-05-15 cleaned up BOM, added connector numbers for Pycubed; cleaned up MPPT add-on BOM
    [Avionics.kicad_sch, Burn_Wires.kicad_sch, Bus_Protection.kicad_sch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]
2024-05-19 Updated component values, iBOM, and schematic printouts
    Pycubed:
    + LT3652 MPP and Imax changes: R10 (MPPT to 20k), R19 (Rsense to 0.27), R16 from 50k to 49.9k
    + Neopixel to 1655
    + SAMD from AU to AF (better temp rating)
    MPPT add-on:
    + connector to HW-09-10-L-D-400-SM
    [Avionics.kicad_sch, MPPT_addon_board.kicad_pcb, MPPT_addon_board.kicad_sch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]
2024-05-19 Burn wire BJT transistor -> MMBT2222A-TP
    [Burn_Wires.kicad_sch, mainboard.kicad_pcb]
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2024-10-16 Updated Pycubed to v08, updated symbol/footprint/3D model libraries
    [18650 battery.step, 1985807.step, 205338-0002.step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]
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2024-10-16 updated z+, picubed folder name, deleted some extra files
    [205338-0004.step, Avionics.kicad_sch, Burn_Wires.kicad_sch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]
2024-10-17 updated flex panels to kicad v08
    [FlexDeploySidePanels.kicad_pcb, FlexDeploySidePanels.kicad_sch, RB160MM-60TR.step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]
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2024-10-19 Change: SAMD replacement started
    Only schematic work performed
    Added RP2350B symbol and footprint along with inductor footprint
    Removed SAMD and placed RP2350B
    RP2350B mostly wired up
    Removed bus protection (busses were split so protection is no longer needed)
    [Avionics.kicad_sch, Power.kicad_sch, RF_and_GPS.kicad_sch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]
2024-10-21 start fixing 2400 board
    [Groundstation_2400_Hat.kicad_pcb, Groundstation_2400_Hat.kicad_sch]
2024-10-21 Change: SAMD replacement part 2
    Upgraded watchdog circuit (needs more analysis)
    Added buttons
    Changed RBF headers to now have RBF_DET pin among other smaller changes
    Fixed some net names
    Fixed some capacitor value's format
    Some other minor changes
    [Avionics.kicad_sch, Burn_Wires.kicad_sch, Connectors.kicad_sch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]
2024-10-26 Change: SAMD replacement part 3
    All schematic work only:
    Modified watchdog circuit, but still needs some work and lots of checking
    Changed VBATT connection on RFB headers
    Upgraded ADCS connector to 12 pins
    [Avionics.kicad_sch, Connectors.kicad_sch, Power.kicad_sch]
2024-10-26 Change: SAMD replacement part 4
    Started layout of new components
    Swapped some pins around on the RP2350B for simpler layout
    [Avionics.kicad_sch, mainboard.kicad_pcb]
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2024-10-31 changed the schottkey diode to the right one and changed footprint of really small resistors
    [LT8491-mezzanine.kicad_pcb, LT8491-mezzanine.kicad_sch]
2024-11-01 Change SAMD replacement part 5
    Schematic is now ready for review
    Watchdog circuit should now work
    Unified some resistor values (fewer resistor bags to find/open)
    Added/fixed some datasheet links
    [Avionics.kicad_sch, Burn_Wires.kicad_sch, Connectors.kicad_sch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]
2024-11-01 Cleanup: removed old files, and printed new schematic
    [mainboard-B_Cu.gbl, mainboard-B_Mask.gbs, mainboard-B_Paste.gbp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]
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2024-11-03 Change: SAMD replacement part 6
    Routing mostly done other than watchdog circuit.
    Fixed some issues like power names
    MCU pinout change for easier routing
    Layer 3 is now mainly 3.3V with a bit of 1.1V and VBAT
    [Avionics.kicad_sch, Connectors.kicad_sch, Power.kicad_sch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]
2024-11-05 Fix: Partial update to title blocks
    Also printed new pdf schematic
    [Avionics.kicad_sch, Burn_Wires.kicad_sch, Connectors.kicad_sch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]
2024-11-06 Updated Board Names & Added DXF file of aluminum structure
    [Coil_Pannel_Z.kicad_pcb, Coil_Pannel_Z.kicad_sch, Coil_Pannel_Z.step]
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2024-11-06 More changes
    Clarified RF jumpers
    USB trace now on one layer (still needs impedance checked)
    General layout cleanup
    [Power.kicad_sch, RF_and_GPS.kicad_sch, mainboard.kicad_pcb]
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2024-11-09 flipped pad for access
    [Coil_Pannel_Z.kicad_pcb]
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2024-11-09 Redesigned 2400
    [Groundstation_2400_Hat.kicad_pcb]
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2024-11-10 Updated correct trace width and spacing
    [Coil_Panel_XY.kicad_pcb, Coil_Pannel_Z.kicad_pcb]
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2024-11-13 updated Holes to remove clearance errors
    [Coil_Pannel_Z.kicad_pcb]
2024-11-13 Fixed 5V traces
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2024-11-13 Updated trace width to .17 to meet specs
    [Coil_Pannel_Z-B_Cu.gbl, Coil_Pannel_Z-B_Mask.gbs, Coil_Pannel_Z-B_Paste.gbp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]
2024-11-13 updated trace widths of non coil to .45
    [Coil_Pannel_Z.kicad_pcb]
2024-11-13 Finished the final adjustments of footprints, final trace width .17
    for future make sure to verify that this will work otherwise we can upsize to .2
    [Coil_Pannel_Z.kicad_pcb]
2024-11-13 Change: changed to different watchdog
    Watchdog change on schematic and layout
    Layout errors mostly taken care of
    Still needs lots of silkscreen fixes
    [Avionics.kicad_sch, Power.kicad_sch, mainboard.kicad_pcb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]
2024-11-14 Added 433 Groundstation, updated 433, battery board (thermistor), and RPi Interface boards
    [433_hat_board.kicad_sch, Groundstation_433_Hat.kicad_pcb, Groundstation_433_Hat.kicad_sch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]
2024-11-16 Fixed labels
    [Groundstation_2400_Hat.kicad_pcb, Groundstation_2400_Hat.kicad_sch]
2024-11-16 Cleanup: picubed silkscreen fixes
    Fixed the picubed silkscreen issues. DRC now passes.
    A couple small touchups to layout, mainly to fix DRC issues.
    Moved some burn wire components to top side for easier assembly.
    Generated an ibom
    [mainboard.kicad_pcb]
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2024-11-20 fixed error from moving
    [Coil_Pannel_Z.kicad_pcb]
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2024-11-20 Cleanup: picuded schematic and silkscreen
    Changed terminal block symbols to be KiCAD default
    External RBF connector silkscreen label updated
    Slight copper adjustment in top left corner
    [Avionics.kicad_sch, Connectors.kicad_sch, mainboard.kicad_pcb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]
2024-11-20 Implemented Changes on Groundstation_2400
    - Added pull down resistors to RXEN, TXEN
    - Fixed up traces
    - Added silk screen labeling
    - Connected the correct voltage (5V vs 3.3V)
    [Groundstation_2400_Hat.kicad_pcb, Groundstation_2400_Hat.kicad_sch, Groundstation_2400_Hat.step]
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2024-11-24 Fixed PiCubed inductor footprints, updated version to 06c
    [Avionics.kicad_sch, Burn_Wires.kicad_sch, Bus_Protection.kicad_sch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]
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2024-12-07 gerbers and picubed silkscreen version resolved
    [Stationary_X_Panel-B_Cu.gbr, Stationary_X_Panel-B_Mask.gbr, Stationary_X_Panel-B_Paste.gbr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]
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2024-12-13 Updated folder/file names and version names where needed, added README
    [Coil_Panel_Z.kicad_pcb, Coil_Panel_Z.kicad_sch, Coil_Panel_Z.step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]
2025-02-19 fixed errors, wiring
    [Coil_Panel_XY.kicad_pcb]
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2025-03-15 fixed traces on thermistor circuit
    [batteryboard.kicad_pcb]
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2025-04-06 Updated PiCubed to KiCad 9 and added JLCPCB jobsets
    [Avionics.kicad_sch, Burn_Wires.kicad_sch, Bus_Protection.kicad_sch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]
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2025-04-06 updated flex panels to kicad 9, PCBWay jobsets, updated JLCPCB jobsets to 4.6 coordinates, moved old boards into old_boards folder
    [2400_TCXO_RPi-B_Cu.gbl, 2400_TCXO_RPi-B_Mask.gbs, 2400_TCXO_RPi-B_Paste.gbp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]
2025-04-06 cleaned up flex panels further, edited jobsets to try running more smoothly
    [FlexDeploySidePanels-B_Cu.gbr, FlexDeploySidePanels-B_Mask.gbr, FlexDeploySidePanels-B_Paste.gbr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]
2025-04-06 updated LT8491-mezzanine (MPPT) to Kicad 9, flex panel schematic PDF name, jobsets back to original ordering (issue was elsewhere)
    [LT8490-B_Cu.gbl, LT8490-B_Mask.gbs, LT8490-B_Paste.gbp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]
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2025-04-07 Revert "Partway through 433 MHz board changes"
    This reverts commit f6f833f81eea78e716a8b2b4156c76b260d993cf.
    [433_hat_board.kicad_sch, Groundstation_433_Hat.kicad_sch, Groundstation_433_Hat.step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]
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2025-04-07 halfway through ADCS board changes. Note backups not included since they are too large
    [ADCS_board-B_Cu.gbl, ADCS_board-B_Mask.gbs, ADCS_board-B_Paste.gbp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]
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2025-04-08 fixing name of ADCS board step
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2025-05-21 fixed magmeter pinout, deleted fiducials, added UART comments on .sch
    [Avionics.kicad_sch, Connectors.kicad_sch, imu_and_magnetometer.kicad_sch]
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2025-06-16 Updated system schematic to correct several errors
    [system.kicad_sch]
2025-08-21 Swap sun pyramid / photodiode yz inputs
    Swap sun pyramid / photodiode yz inputs
    - Sun pyramids (8) -> RP3250B ADC pins
    - Photodiode yz (8) -> ADS7830 ADC
    - Logic behind this: RP2350B ADC has higher fidelity than ADS7830, and the yz photodiodes point in redundant directions so that's a waste.
    [ADC_multiplexer.kicad_sch, Avionics.kicad_sch]
2025-08-21 Add 3.3v reference voltage to ADS7830
    Add 3.3v reference voltage to ADS7830
    - V_REF_RP2350B_ADC = 3.3v (can't change), V_REF_ADS7830 = 2.5v (internal)
    - This requires us to clip readings from the RP2350B ADC in the code
    - Since the ADS7830 can accept an external reference voltage, I've connected it up to the 3.3v bus to circumvent those reading issues :)
    referenced adafruit ads7830 breakout board circuit for edits (link)[https://github.com/adafruit/Adafruit-ADS7830-PCB/tree/main]
    [ADC_multiplexer.kicad_sch]
2025-08-21 Revert "Add 3.3v reference voltage to ADS7830"
    This reverts commit 95aaf1d56cf3acd9444d3f2bc4515d7420654ed3.
    [ADC_multiplexer.kicad_sch]
2025-08-21 Revert "Swap sun pyramid / photodiode yz inputs"
    This reverts commit 476f3e609712227db83ea3ec49a2480c44b72f0a.
    [ADC_multiplexer.kicad_sch, Avionics.kicad_sch]
2025-08-21 Sun sensor fixes (schematic)
    1. Swap sun pyramid / photodiode yz inputs
    2. Add 3.3v reference voltage to ADS7830
    referenced adafruit ads7830 breakout board circuit for edits (link)[https://github.co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
    [ADC_multiplexer.kicad_sch, Avionics.kicad_sch]
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2025-08-21 Fix silkscreen
    had to remove the fish, sorry sage :(
2025-08-21 Add watchdog 6v regulator
    To schematic, still needs added on pcb. Schematic needs to be checked idk what I'm doing lol
    [watchdog.kicad_sch]
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2025-08-23 Fix schottky direction on schematic
    [watchdog.kicad_sch]
2025-08-23 Fix shottky orientation on pcb
    [mainboard.kicad_pcb]
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2025-08-24 Minor schematic edits
    - add schottky diode to 3.3v net - prevents blowing up the board 💀
    - schematic cleanup (e.g., overwritten text)
    - fix magnetometer naming conventions (magmeter >> magnmeter)
    [Avionics.kicad_sch, Power.kicad_sch, imu_and_magnetometer.kicad_sch]
2025-08-24 Minor pcb edits
    - add schottky diode to 3.3v
    - add fiducials
    - reduce solder paste on u5 (prevent floating)
    - fix 1v1 routing on chip (prev version made soldering difficult)
    - refix magnetometer naming conventions (magmeter >> magnmeter)
    [imu_and_magnetometer.kicad_sch]
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2025-08-24 Reduce default trace width from 0.25mm -> 0.23495mm
    Makes the MCU pins less prone to shorts. These are the netclass sizes used on picubed fwiw
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2025-08-28 Give vias clearance
    Prevent net shorts
    [mainboard.kicad_pcb]
2025-08-29 Final edits
    - Schematic: notes
    - Fixed version names + date
    [Avionics.kicad_sch, Burn_Wires.kicad_sch, Bus_Protection.kicad_sch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]
2025-09-01 Fixed USB-C Connector
2025-09-01 Resolve merge: drop KiCad autosave/lock files; add .gitignore
    [Avionics.kicad_sch, Burn_Wires.kicad_sch, Bus_Protection.kicad_sch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]
2025-09-01 Fixed: Connector Footprint
2025-09-01 Fixed all USBCs from root. Light work no reaction :D
    [motor_board.kicad_pcb, picubed_samwise.kicad_pcb]
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2025-12-03 VBATT trace position fix
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2026-03-08 Revert cut
